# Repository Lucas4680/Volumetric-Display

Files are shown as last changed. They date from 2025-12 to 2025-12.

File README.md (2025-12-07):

# Volumetric-Display
A 3D display that utilizes a spinning transparent OLED. This is a version 2 overhaul of a previous project that did not work. Before, I had too little knowledge going into the project to pull off a working design. However, this time, I have completely changed the designs, PCB, and working principles for a much better and more solid display. At its core, it's a transparent OLED that rotates using a brushed motor. At each slice in its rotation, it displays a frame of a 3D image. As it spins, due to peristence of vision (the eye retains light for slightly longer than it exists), at high enough speeds, it looks like a solid 3D display. Below is the BOM as well as images of each component. Check out the journal to see my process of creating this project!

Total Grant - $59.07:

EasyEDA PCB - $5.30:





Aliexpress - $31.10:



LCSC - $22.67:



Final CAD Assembly:





PCB & Schematic:









Full Assembly Render:

Volumetric_2025-Dec-06_03-30-14AM-000_CustomizedView7592079908_jpg (1)

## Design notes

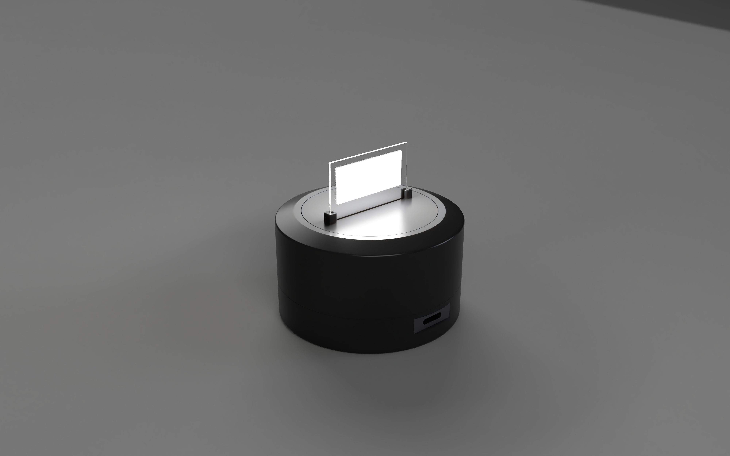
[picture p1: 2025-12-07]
CAD/Render.jpg

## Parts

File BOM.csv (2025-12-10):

1 | No Purchase | AKIB-PAD-THT | VIN+,VIN-,VOUT+,VOUT-,M+,M-,P+,P- | PADPAD | 8 |  |  |  |  |  | 1
2 | Purchase | A3144EUA-T-JSM | U1 | TO-92S-3_L4.1-W1.7-P1.27-L | 1 | A3144EUA-T-JSM | JSMSEMI(杰盛微) | LCSC | C18188954 | 0.238 | 3 | https://item.szlcsc.com/product/jpg_256473_0.html
3 | No Purchase | ESP32-WROOM-32_M103QH3200PH3Q0_ | IC2 | ESP32S3WROOM1N16R8 | 1 |  | Espressif Systems |  |  |  | 49
4 | Purchase | 1000uF | C10,C11 | CAP-SMD_L7.3-W4.3-R-RD | 2 | TAJE108M006RNJ | Kyocera AVX | LCSC | C54883 | 2.354 | 2 | https://item.szlcsc.com/91116.html
5 | No Purchase | 4.7uF | C14,C2,C5 | C1206 | 3 | CS3216X7R475K500NRI | SAMWHA(三和) | LCSC | C513768 | 0.034 | 2 | https://item.szlcsc.com/89171.html
6 | Purchase | AO3400A_C5224194 | Q2 | SOT-23-3_L3.0-W1.6-P1.90-LS2.8-BR | 2 | AO3400A | ElecSuper(静芯) | LCSC | C5224194 | 0.022 | 3 | https://atta.szlcsc.com/upload/public/pdf/source/20200309/C150720_EA5FFAC42CC5D7D051BA246B6393078B.pdf
7 | No Purchase | 10kΩ | R8,R6,R7 | RES-TH_BD1.8-L3.2-P7.20-D0.4 | 3 | MF1/8W-10KΩ±1% T | CCO(千志电子) | LCSC | C119202 | 0.01 | 2 | https://item.szlcsc.com/120430.html
8 | No Purchase | 100kΩ | R17,R14 | RES-TH_BD1.8-L3.2-P7.20-D0.4 | 2 | MF1/8W-10KΩ±1% T | CCO(千志电子) | LCSC | C119202 | 0.01 | 2 | https://item.szlcsc.com/120430.html
9 | Purchase | MCP6546UT-I/LT | U2 | SC-70-5_L2.0-W1.3-P0.65-LS2.1-BL | 1 | MCP6546UT-I/LT | MICROCHIP(美国微芯) | LCSC | C623505 | 0.891 | 5 | https://www.ti.com/cn/lit/ds/symlink/sn74ahct1g126-q1.pdf?ts=1627545605239
11 | No Purchase | 1kΩ | R9 | RES-TH_BD1.8-L3.2-P7.20-D0.4 | 1 | MF1/8W-10KΩ±1% T | CCO(千志电子) | LCSC | C119202 | 0.01 | 2 | https://item.szlcsc.com/120430.html
12 | No Purchase | TSG002A06026A | BOOT,EN/RST | SW-SMD_4P-L6.2-W6.2-P4.50-LS9.2 | 2 | TSG002A06026A | BZCN(博众电气) | LCSC | C2888623 | 0.046 | 4 | https://atta.szlcsc.com/upload/public/pdf/source/20210826/6648073D61182C9EF5B860CFE83950B8.pdf
13 | Purchase | 10kΩ | CURRENT | RES-ADJ-SMD_3P-L3.0-W3.8-P1.75-BR | 1 | TC33X-2-103E | BOURNS | LCSC | C719176 | 0.099 | 3 | https://item.szlcsc.com/762158.html
14 | No Purchase | 2.73kΩ | R11 | RES-TH_BD1.8-L3.2-P7.20-D0.4 | 1 | MF1/8W-10KΩ±1% T | CCO(千志电子) | LCSC | C119202 | 0.01 | 2 | https://item.szlcsc.com/120430.html
15 | No Purchase | 130Ω | R13 | RES-TH_BD1.8-L3.2-P7.20-D0.4 | 1 | MF1/8W-10KΩ±1% T | CCO(千志电子) | LCSC | C119202 | 0.01 | 2 | https://item.szlcsc.com/120430.html
16 | No Purchase | 100Ω | R1 | RES-TH_BD1.8-L3.2-P7.20-D0.4 | 1 | MF1/8W-10KΩ±1% T | CCO(千志电子) | LCSC | C119202 | 0.01 | 2 | https://item.szlcsc.com/120430.html
17 | No Purchase | 0.1u | C12,C13,C1,C3,C7,C8,C9 | _0402 | 7 | CS1005X7R104K500NR | Samwha Capacitor | LCSC | C513772 | 0.002 | 2 | https://www.lcsc.com/product-detail/Multilayer-Ceramic-Capacitors-MLCC-SMD-SMT_Samwha-span-style-background-color-ff0-Capacitor-span-CS1005X7R104K500NR_C51377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
18 | No Purchase | TJ-S1608SW9T6ALC2R-A5 | HALL,MOTOR,VDD | LED0603-RD_RED | 3 | TJ-S1608SW9T6ALC2R-A5 | TOGIALED(统佳) | LCSC | C601657 | 0.047 | 2 | https://item.szlcsc.com/221679.html
19 | Purchase | 50mΩ | R10 | R2512 | 1 | VMS-R050-1.0-U | Isabellenhuette(伊萨普兰) | LCSC | C2688871 | 0.851 | 2 | https://item.szlcsc.com/347967.html
20 | No Purchase | 560Ω | R15 | R0603 | 1 | PTFR0603B150RN9 | RESI(开步睿思) | LCSC | C2692872 | 0.18 | 2 | https://www.mouser.in/datasheet/2/447/PYu_RT_1_to_0_01_RoHS_L_11-1669912.pdf
21 | No Purchase | 150Ω | R16,R2 | R0603 | 2 | PTFR0603B150RN9 | RESI(开步睿思) | LCSC | C2692872 | 0.18 | 2 | https://www.mouser.in/datasheet/2/447/PYu_RT_1_to_0_01_RoHS_L_11-1669912.pdf
22 | Purchase | INA180A2IDBVT | U6 | SOT-23-5_L3.0-W1.7-P0.95-LS2.8-BR | 1 | INA180A2IDBVT | TI(德州仪器) | LCSC | C116203 | 0.242 | 5 | https://item.szlcsc.com/236104.html
23 | Purchase | 1N5819HW | D1 | SOD-123_L2.7-W1.6-LS3.7-RD-1 | 1 | 1N5819HW | TECH PUBLIC(台舟) | LCSC | C2905649 | 0.021 | 2 | https://atta.szlcsc.com/upload/public/pdf/source/20210423/C2828417_EF1BF8BE3D48F97E320B09B073C89160.pdf
24 | No Purchase | 5.1kΩ | R4,R5 | R0805 | 2 | RTT05512JTP | RALEC(旺诠) | LCSC | C104384 | 0.002 | 2 | https://item.szlcsc.com/142685.html
25 | No Purchase | 10uF | C4 | C1210 | 1 | CS3225X7R106K500NRL | SAMWHA(三和) | LCSC | C2918502 | 0.073 | 2 | https://item.szlcsc.com/364452.html
26 | No Purchase | 1uF | C6 | C0402 | 1 | TCC0402X5R105M100AT | CCTC(三环) | LCSC | C2887020 | 0.002 | 2 | https://item.szlcsc.com/15869.html
27 | No Purchase | HX PZ2.54-1X7P ZZ | H2 | HDR-TH_7P-P2.54-V-M | 1 | HX PZ2.54-1x7P ZZ | hanxia(韩下) | LCSC | C32713273 | 0.044 | 7 | https://item.szlcsc.com/502962.html
28 | No Purchase | 10kΩ | R3 | R0603 | 1 | RC0603FR-0710KL | YAGEO(国巨) | LCSC | C98220 | 0.001 | 2 | https://www.mouser.in/datasheet/2/447/PYu_RT_1_to_0_01_RoHS_L_11-1669912.pdf
29 | No Purchase | LD1117-3.3 | U3 | SOT-223_L6.7-W3.5-P2.30-BR | 1 | LD1117-3.3 | UMW(友台半导体) | LCSC | C347229 | 0.044 | 4 | https://item.szlcsc.com/245102.html
30 | Purchase | HX TYPE-C 24P QT | USB1 | USB-C-SMD_HX-TYPE-C-24P-QT | 1 | HX TYPE-C 24P QT | hanxia(韩下) | LCSC | C5178546 | 0.305 | 30 | https://atta.szlcsc.com/upload/public/pdf/source/20220923/D25CF69580F5563A5BDCE103720011DF.pdf

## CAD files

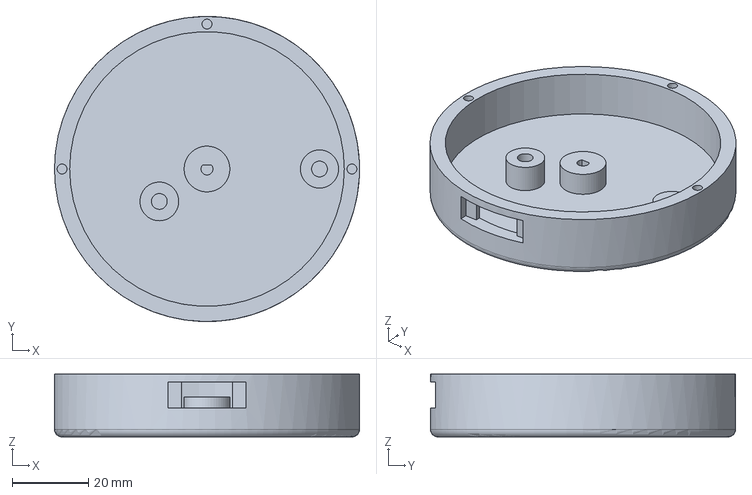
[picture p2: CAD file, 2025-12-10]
CAD/Lower Shell.step
80.0 x 80.0 x 16.5 mm

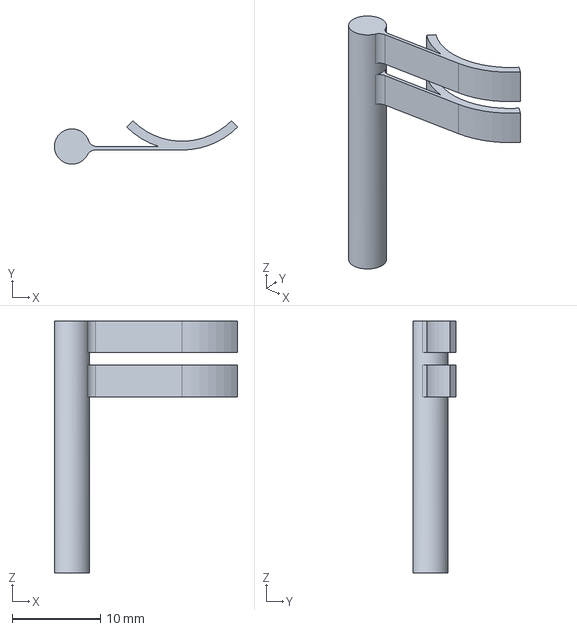
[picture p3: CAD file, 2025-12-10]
CAD/Brush.step
20.8 x 4.91 x 28.6 mm

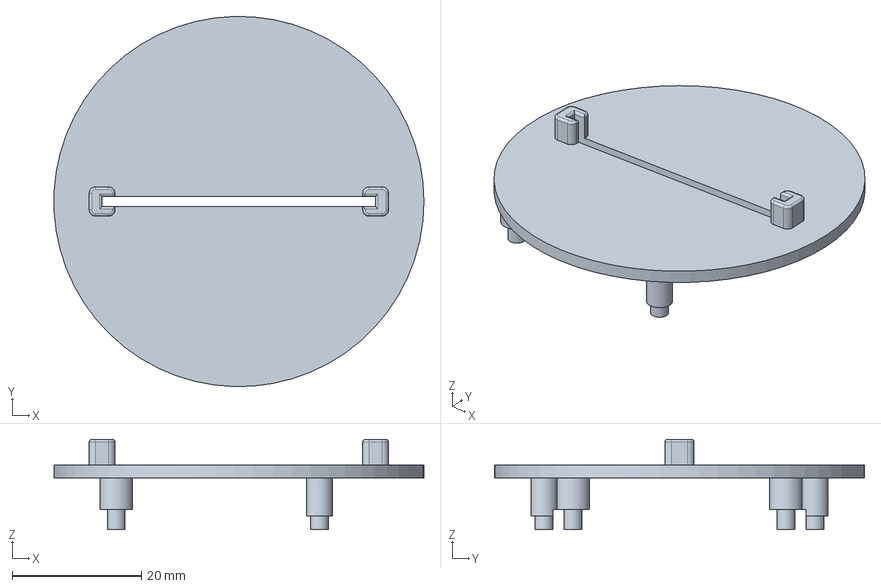
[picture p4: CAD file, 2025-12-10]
CAD/Screen Mount.step
57.4 x 57.4 x 14.0 mm

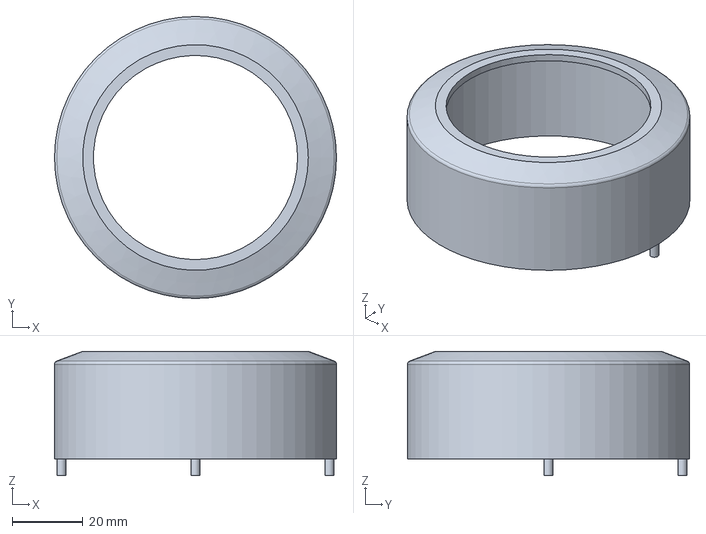
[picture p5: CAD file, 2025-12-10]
CAD/Upper Shell.step
80.0 x 80.0 x 35.3 mm

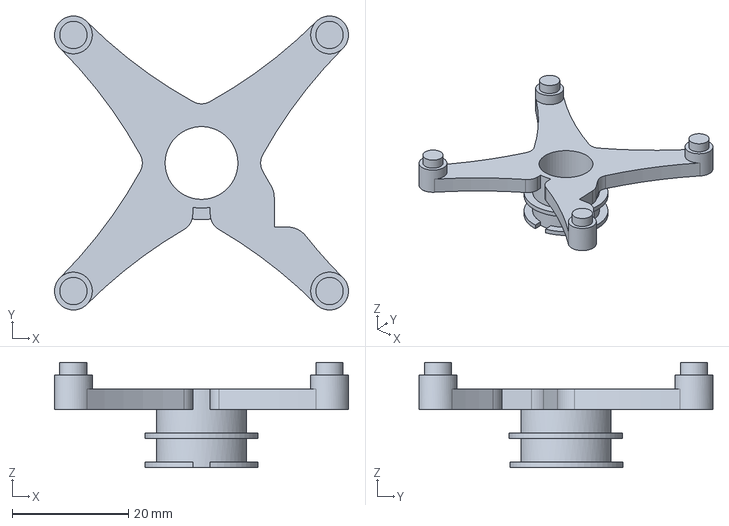
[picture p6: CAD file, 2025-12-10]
CAD/Motor Mount.step
50.5 x 50.5 x 18.1 mm

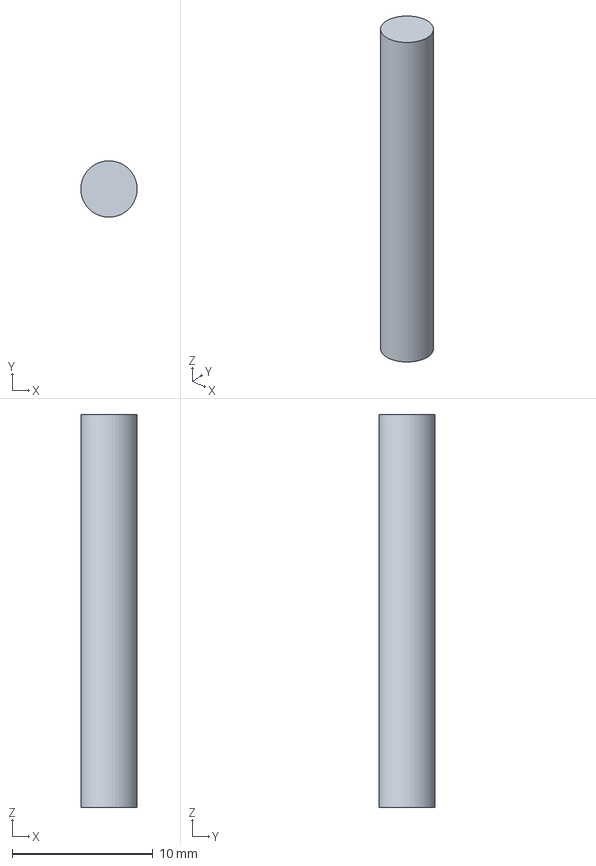
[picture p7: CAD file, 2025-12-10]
CAD/Magnet Mount.step
4.00 x 4.00 x 27.9 mm

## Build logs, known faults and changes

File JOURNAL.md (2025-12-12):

<!--
  ===================    !!READ THIS NOTICE!!   ====================
  DO NOT edit this file manually. Your changes WILL BE OVERWRITTEN!
  This journal is auto generated and updated by Hack Club Blueprint.
  To edit this file, please edit your journal entries on Blueprint.
  ==================================================================
-->

## 10/19/2025 - Recap of Past Work  

Over the course of the past few months, I've started brainstorming, researching, and building this project. So far, I've designed a first PCB design and spent countless time dealing with the many issues with this design. I've managed to get the display working but have decided to nearly completely redo the project building on all the knowledge I've gained from this first trial. Most of these issues came from lack of experience in PCB design and electronics. 



(I would like to note that the rest of this project will be almost completely new and only build off past work)  

## 10/24/2025 - Motor and Power Delivery Research and Testing  

I began by testing the previous 5v dc motor I had to see if it could rotate fast enough and with enough torque. I found that it did have enough speed to create the persistence of vision effect. Then I tested the power delivery contacts (5v power from usb has to travel up to the rotating pcb housing the mcu, screen, motor, etc) and found that they were too spotty and caused too much friction for the motor to keep up with.

I then researched potential new methods of transferring power (slip rings - not reliable and rated for fast speeds, capacitive coupling - too finicky and unrealistic to set up, and wireless - again unrealistic to implement) but concluded that sliding contacts were still the best way forward. I also researched potential new motors that could handle the extra friction. I found a 12v motor with gearbox attached that gives promising results. In addition, I researched different ways to create the sliding contacts, carbon brushes, copper brushes, and pogo pins among others.

Previous motor test at speed:


## 10/28/2025 - Further Research  

Continued researching the redesigns that were necessary. Began by reworking the power transfer from usb into the rotating pcb, decided on using concentric rings of copper tape (or similar) that wrap around the motor, with brush contacts pressed onto it from the stator. Also settled on using a hall effect sensor with multiple magnets in the base to more accurately capture rotational data. Slices of the image can then be interpolated more accurately from these readings. I also learned that ESP32S3 has a function for digital interrupts that has no overhead on the CPU.



## 11/18/2025 - Completed PCB

Drew, Wired, and Routed the PCB. Creating a circuit to limit the amount of current was a big challenge. Due to the limited USB power I have onboard, if the motor draws overcurrent for even a fraction of a second, the entire board can brown or black out. Thus, I implemented a fast acting current trip using a shunt resistor that also triggers interrupt on the MCU to hold the motor off. This took many iterations on schematics and parts before arriving to a hopefully working circuit. The rest of the board required planning for mounting as well as part placement to ensure a balanced board with a center of gravity over the motor. Otherwise, rotation would cause vibrations. I also consulted with teachers and instructors on my robotics team regarding my layouts and designs. 

Overall the entire process took a lot of iteration and realizations of how little I knew and how much I had to revise.




## 11/20/2025 - PCB Revisions

After importing the PCB into fusion and beginning modeling the 3d printed parts, I began to run into issues with the placement of parts getting in the way of supports. Thus I revised the PCB with these issues in mind. This did throw off the center of gravity a little but some tuning once the board is finished will account for it (I left pads to add weight on).



# 11/30/2025 - CAD

I began by cadding the joint  between the motor and the PCB, which was somewhat difficult since I had to avoid all the components on the PCB. Then I created the OLED mount on the other side of the PCB. For the outside shell, I created a simple enclosure that accepts the motor shaft at the bottom. The case is split into a lower and upper module to make assembly and modifying easier. The custom slip ring that transfers power from stationary USB to the rotating PCB was the most difficult part to make. From previous research, I determined it would be best to use a conductive tape and some sort of brush. There wasn't much usable space around the body of the motor to create the rings but I managed to find a solution that would work pretty well. I opted in the end to have the brush also made of the same conductive tape and create a 90 degree arc around the motor to increase contact area. It's tensioned with a small spring made from 3d printed material. This would make it easy to tune the strength by rotating around the pivot.

Render:

Volumetric_2025-Nov-29_07-59-37PM-000_CustomizedView14745335757_png

Slice: 



Brush (The center circle is the motor + conductive ring):



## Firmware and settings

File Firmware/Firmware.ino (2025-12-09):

#include "driver/gpio.h"
#include "soc/gpio_struct.h"
#include "soc/gpio_reg.h"
// Libraries
#include <Adafruit_SSD1306.h>
#include <Adafruit_GFX.h>
#include <SPI.h>

// OLED screen resolution
#define SCREEN_WIDTH 128 
#define SCREEN_HEIGHT 64 

// OLED SPI pin definitions
#define OLED_MOSI  15
#define OLED_CLK   5  
#define OLED_DC    10  
#define OLED_RESET 3
#define OLED_CS    13 

// Initialize OLED display object
Adafruit_SSD1306 Oled(SCREEN_WIDTH, SCREEN_HEIGHT, &SPI, OLED_DC, OLED_RESET, OLED_CS);

#define DC_HIGH  (GPIO.out_w1ts = (1UL << OLED_DC))
#define DC_LOW   (GPIO.out_w1tc = (1UL << OLED_DC))
#define CS_HIGH  (GPIO.out_w1ts = (1UL << OLED_CS))
#define CS_LOW   (GPIO.out_w1tc = (1UL << OLED_CS))
// #define DC_HIGH  digitalWrite(OLED_DC,HIGH);
// #define DC_LOW  digitalWrite(OLED_DC,LOW);
// #define CS_HIGH  digitalWrite(OLED_CS,HIGH);
// #define CS_LOW  digitalWrite(OLED_CS,LOW);
uint8_t buffer[SCREEN_WIDTH * (SCREEN_HEIGHT / 8)];

void sendCommand(uint8_t cmd) {
  SPI.transfer(cmd);
}

void sendData(uint8_t data) {
  SPI.transfer(data);
}

// Set a pixel ON or OFF and update OLED immediately
void drawPixelFast(int x, int y, bool color) {
  if (x < 0 || x >= SCREEN_WIDTH || y < 0 || y >= SCREEN_HEIGHT) return;

  int page = y / 8;
  int bit = y % 8;
  int index = page * SCREEN_WIDTH + x;

  if (color)
    buffer[index] |= (1 << bit);
  else
    buffer[index] &= ~(1 << bit);

  // Update just this byte on OLED
  
  //CS_LOW;
  uint8_t cmds[3] = { 0xB0 + page, 0x00 + (x & 0x0F), 0x10 + ((x >> 4) & 0x0F) };
  DC_LOW;
  SPI.transfer(cmds, 3); // send all commands at once
  DC_HIGH;
  SPI.transfer(buffer[index]);            // Send updated byte
  //CS_HIGH;
}


void setup() {
  delay(1000);


  Serial.begin(9600);
  SPI.begin(OLED_CLK, -1, OLED_MOSI, OLED_CS);

  Serial.println("a!");
  pinMode(OLED_RESET, OUTPUT);
  digitalWrite(OLED_RESET, LOW);
  delay(50);
  digitalWrite(OLED_RESET, HIGH);
  delay(50);

  // Initialize the OLED display
  if(!Oled.begin(SSD1306_SWITCHCAPVCC)) {
    Serial.println(F("SSD1306 allocation failed"));
    while (true) {Serial.println("nope");}
  }
  // for (int i = 0; i < 10; i++) {
  //   Serial.println("yes!");
  //   delay(1000);
  // }
  // Set display text size and color, then clear the screen
  Oled.ssd1306_command(SSD1306_SETCONTRAST);
  Oled.ssd1306_command(0xFF);  // Max contrast
  Oled.setRotation(0);
  Oled.invertDisplay(false);

  Oled.clearDisplay();
  Oled.setCursor(0, 0);
  Oled.setTextSize(2);
  Oled.setTextColor(WHITE);
  Oled.display();
  delay(1000);
  Oled.println("Hi");
  delay(1000);

      // Display the content
  CS_LOW;

  while(true) {
    for(int i = 0; i < SCREEN_WIDTH; i++) {
      for (int x = 0; x < SCREEN_HEIGHT; x++) {
        // Oled.drawPixel(i, x, SSD1306_INVERSE);
        // Oled.display();
        drawPixelFast(i, x, true); 
        //delay(10);
      }
    }
    //delay(1000);
    for(int i = 0; i < 128; i++) {
      for (int x = 0; x < 64; x++) {
        drawPixelFast(i, x, false); 
        //delay(10);
      }
    }
  }
}

float t = 0;  // Time variable for animation

void loop() {

}

// NOTE: This firmware currently just cycles through each pixel on the dispay to make sure the PCB works. Extensive code will be written later as it's really hard without having the device to rapidly test on.
